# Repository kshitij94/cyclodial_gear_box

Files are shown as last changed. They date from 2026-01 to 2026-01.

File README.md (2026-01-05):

This repo contains all the solidworks files required for 3d printing the cycloidal drive.
It also contains the ball bearings. These ball bearing uses 4.5 mm bearing balls: amazon.com/dp/B07YKLXJLQ?ref=ppx_yo2ov_dt_b_fed_asin_title

Theory about cycloidal drive can be found here:
https://www.youtube.com/watch?v=OsS9-FzKN6s
https://uwaterloo.atlassian.net/wiki/spaces/UWRT/pages/33962263427/Cycloidal+Drive+-+Rev+1+Prototype+Journal
https://www.youtube.com/watch?v=Nk3aaVcvbpA

the main doc to follow to build the gear is a "Cycloidal Drive – StepByStep Robotics" (https://stepbystep-robotics.com/hp/robots/cycloidal-drive/)
 pdf uploaded in this repo.

To design the cyclodial drive gear in solidworks, the main idea is to first create a plan sketch, which contains the disk, housing pins, output shaft pins, input shaft and its essentric component. Then copy paste this plan to build each individual components for 3d printing. After copying the plan sketch onto a new part in solidworks, delete the sketch that are not needed and then do the extrudus. The videos and other designs always create two disk 180 apart. That is done to reduce wear when the motor is runing super fast. But for our usecase the motor rotates slow and hence we only need 1 disk. It simplified the design and assembly by a lot.

The values for this drive are:

R =  63 
E=2 
Rr=5 
N=22

“R” is the radius of the Rotor/PCD of rollers
“E” is the eccentricity (or offset)
“Rr” is the radius of the Rollers
“N” which is the number of Rollers

Electrical components:

I used nema17: https://www.amazon.com/dp/B00PNEQKC0?ref=ppx_yo2ov_dt_b_fed_asin_title

controller used: https://www.amazon.com/dp/B0CP92T4QR?ref=ppx_yo2ov_dt_b_fed_asin_title

the current limit on the controller is set to 0.75. Although the motor can take 2 amp, setting the controller current limit to 1 amp caused the motor motion to break. But after setting to 0.75, the motion was continous.

This repo also contains the arduino code for controlling the motor.

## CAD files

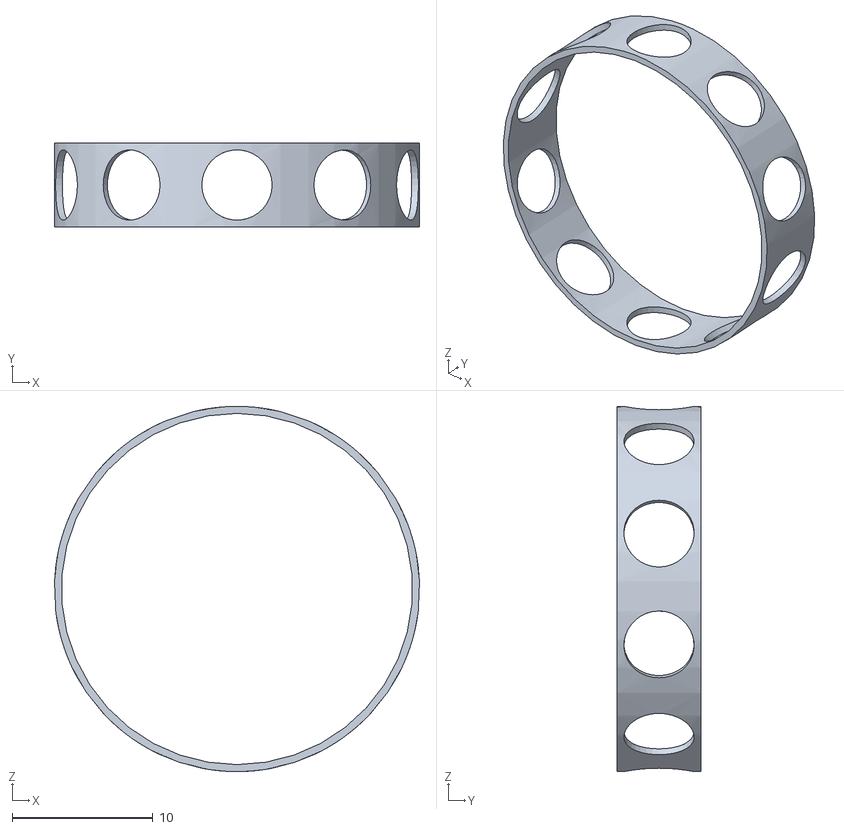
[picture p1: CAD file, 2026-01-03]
ball_bearing_ID_90/assembly - divider-1.STL
26.0 x 6.00 x 26.0

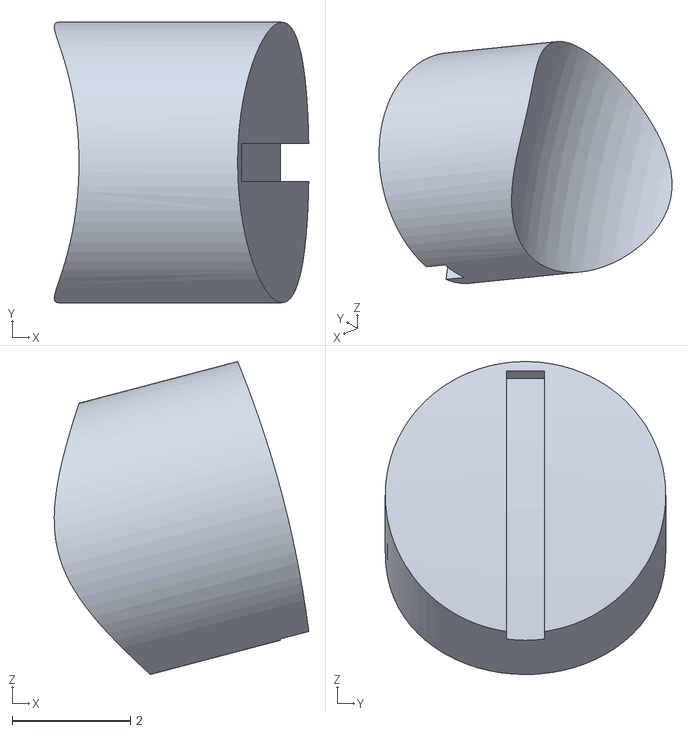
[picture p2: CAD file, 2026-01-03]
ball_bearing_ID_90/stl/assembly - stopper-1.STL
4.31 x 4.75 x 5.30

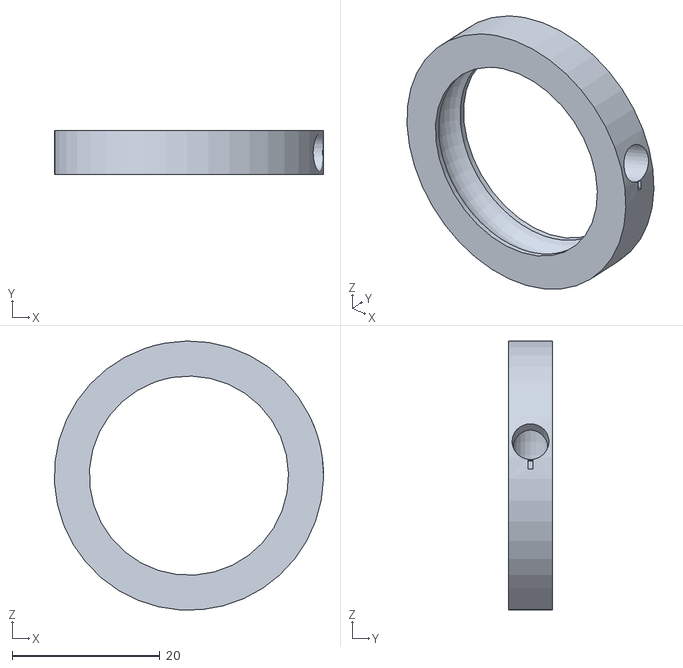
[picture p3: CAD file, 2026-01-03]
ball_bearing_ID_20/assembly - outer_casing-2.STL
36.5 x 6.00 x 36.5

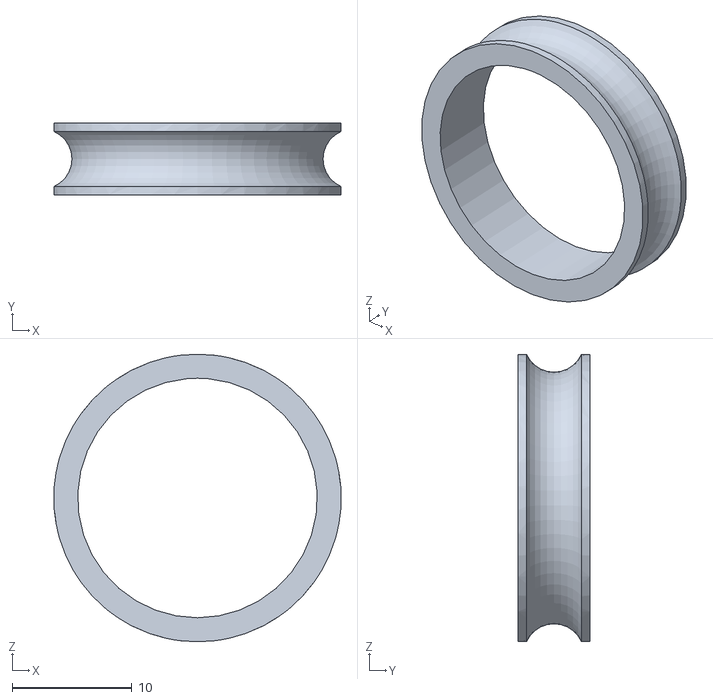
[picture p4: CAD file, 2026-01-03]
ball_bearing_ID_90/assembly - inner_casing-1.STL
24.0 x 6.00 x 24.0

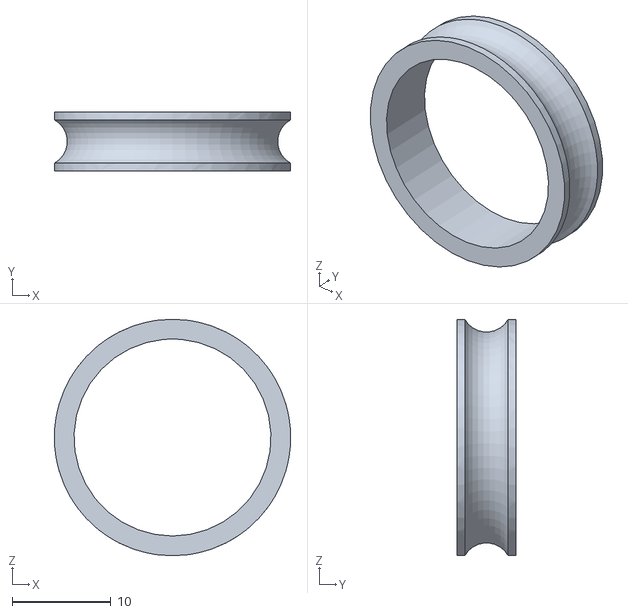
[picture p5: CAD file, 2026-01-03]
ball_bearing_ID_90/stl/assembly - inner_casing-1-1.STL
24.0 x 6.00 x 24.0

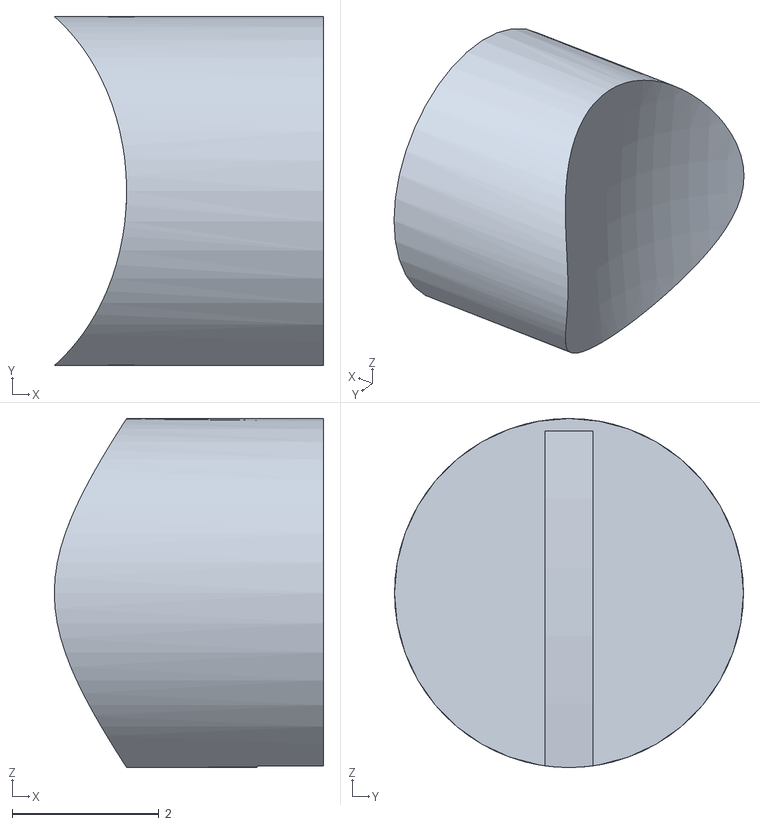
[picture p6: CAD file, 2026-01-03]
ball_bearing_ID_90/stl/assembly - stopper-2.STL
3.67 x 4.75 x 4.75

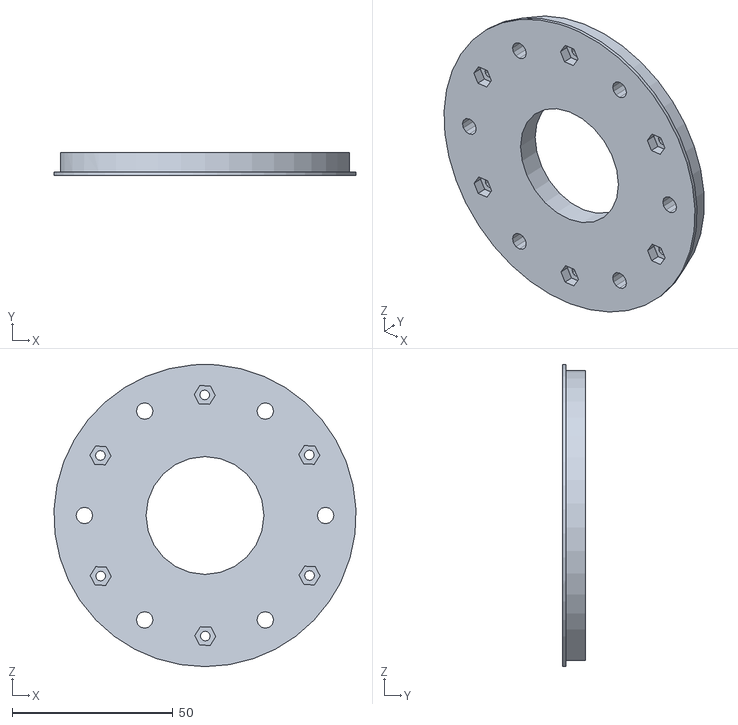
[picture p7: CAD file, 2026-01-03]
cycloidal_drive_attemp_3/stl/output_shaft_2.STL
93.9 x 7.00 x 94.0

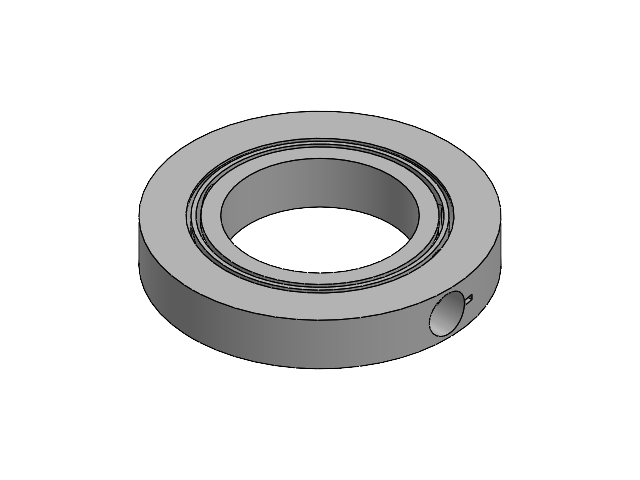
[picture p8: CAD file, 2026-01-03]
ball_bearing_ID_20/assembly.SLDASM
divider
inner_casing
outer_casing

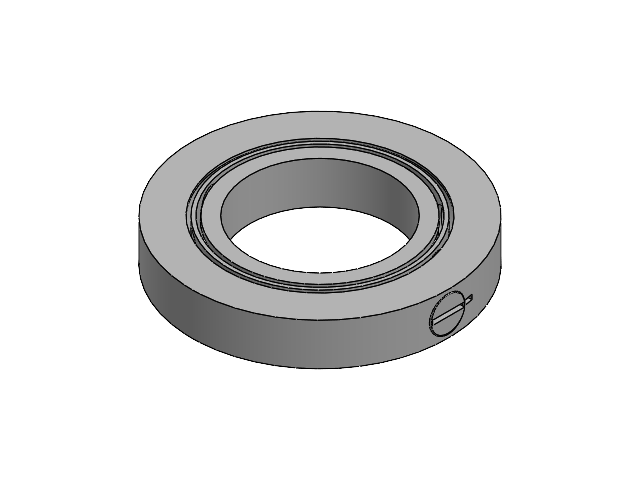
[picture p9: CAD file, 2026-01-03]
ball_bearing_ID_90/assembly.SLDASM
divider
inner_casing
outer_casing
stopper

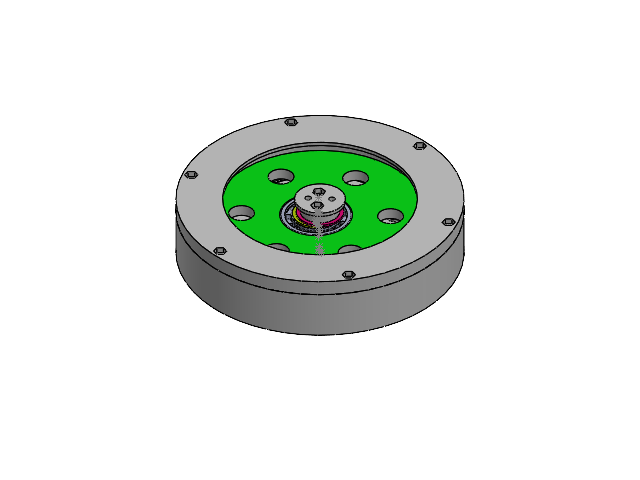
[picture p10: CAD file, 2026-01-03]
cycloidal_drive_attemp_3/Assem2.SLDASM
housing_tmp
i90
ID20 x 3
input_shaft1
input_shaft_2
output_shaft_1
input_shaft_3
disk
input_shaft_4
input_shaft_5
input_shaft_6_1
output_side_cover
input_shaft_0
motor_housing

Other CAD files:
ball_bearing_ID_90/stl/assembly - outer_casing-3.STL
ball_bearing_ID_90/stl/assembly - divider-1-1.STL
ball_bearing_ID_20/stl/26-dec - outer_casing-3.STL
ball_bearing_ID_20/stl/26-dec - divider-1.STL
ball_bearing_ID_20/divider.SLDPRT
ball_bearing_ID_20/inner_casing.SLDPRT
ball_bearing_ID_20/outer_casing.SLDPRT
ball_bearing_ID_20/stl/26-dec - inner_casing-1.STL
ball_bearing_ID_20/stl/assembly - outer_casing-2.STL
ball_bearing_ID_20/stl/inner_casing.STL
ball_bearing_ID_20/stl/outer_casing.STL
ball_bearing_ID_20/stl/stopper.STL
ball_bearing_ID_20/stopper.SLDPRT
ball_bearing_ID_90/divider.SLDPRT
ball_bearing_ID_90/inner_casing.SLDPRT
ball_bearing_ID_90/outer_casing.SLDPRT
ball_bearing_ID_90/stl/90 - divider-1.STL
ball_bearing_ID_90/stl/90 - inner_casing-1.STL
ball_bearing_ID_90/stl/90 - outer_casing-3.STL
ball_bearing_ID_90/stl/90 - stopper-2.STL
ball_bearing_ID_90/stl/90_1 - divider-1.STL
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

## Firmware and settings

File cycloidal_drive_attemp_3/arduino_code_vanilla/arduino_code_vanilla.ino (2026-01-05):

#include <AccelStepper.h>

// Define pin connections & motor's steps per revolution
const int dirPin = 2;
const int stepPin = 3;
int enable = 1;
void setup()
{
  delay(1000);
  // Declare pins as Outputs
  pinMode(stepPin, OUTPUT);
  pinMode(dirPin, OUTPUT);
  digitalWrite(dirPin, HIGH);
  delay(1000);
}

void loop()
{
  if (enable == 0)
  {
    return;
  }

  for (int i = 0; i < 200; i++)
  {
    digitalWrite(stepPin, HIGH);
    delayMicroseconds(500);
    digitalWrite(stepPin, LOW);
    delayMicroseconds(500);
  }

  for (int i = 0; i < 200; i++)
  {
    digitalWrite(stepPin, HIGH);
    delayMicroseconds(500);
    digitalWrite(stepPin, LOW);
    delayMicroseconds(500);
  }
}

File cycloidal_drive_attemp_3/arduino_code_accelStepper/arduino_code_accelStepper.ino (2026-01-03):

#include <AccelStepper.h>
const int dirPin = 2;
const int stepPin = 3;

// 1 = Driver interface (Step/Dir pins)
AccelStepper stepper(1, stepPin, dirPin); 

void setup() {
  stepper.setMaxSpeed(800);    // Try starting here (250us total delay equivalent)
  stepper.setSpeed(600); // Ramps up the speed so it doesn't stall
}

void loop() {
  stepper.runSpeed();
}
